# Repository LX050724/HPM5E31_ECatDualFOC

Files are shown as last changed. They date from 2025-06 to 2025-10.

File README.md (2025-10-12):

# 基于HPM5E31的双路EtherCAT高性能高精度FOC驱动板

仓库使用lfs，不能直接下载zip，jlink版本需要v10以上

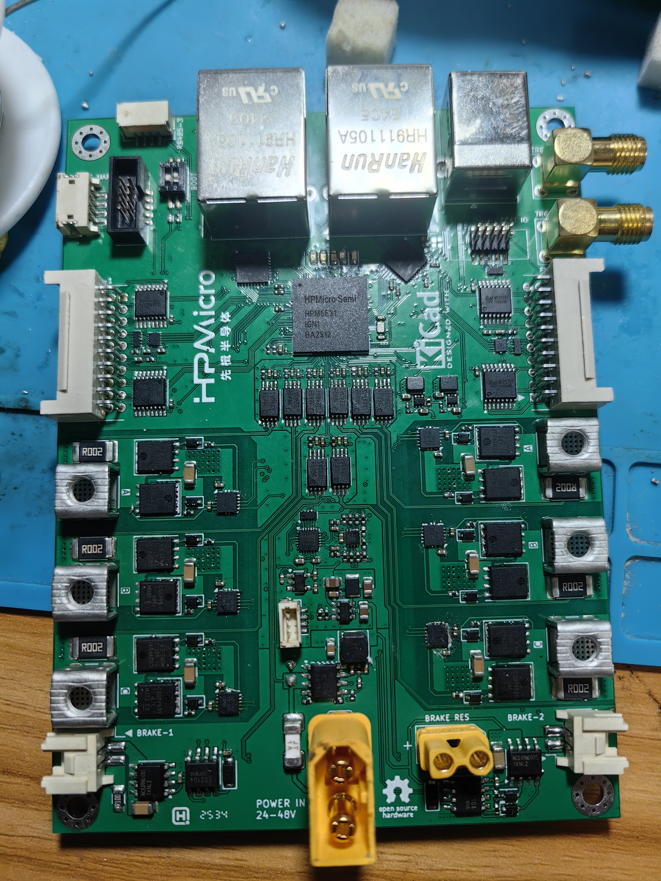
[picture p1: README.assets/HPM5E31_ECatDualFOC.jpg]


## 产品规格：

| 支持电机数 | 2路 |
| --- | --- |
| 动力电源 | 24VDC~60VDC |
| 额定输出电流 | 20Arms |
| 峰值输出电流 | 未测试 |
| 急停按钮 | 光耦输入，支持常开式或常闭式接线或外部电源控制<br />支持硬件安全扭矩关断（SOT） |
| 反馈信号 | 差分ABZ<br />差分UVW<br />基于SPI接口的编码器（抗干扰弱）<br />基于高速485接口的编码器如多摩川<br />电机温度NTC |
| 能耗制动 | 可外接制动电阻 |
| 抱闸 | 支持，最大电流1A，支持电流测量 |
| 冷却方式 | 可选的板载散热器和风扇主动散热 |
| 脉冲方向控制 | 复用ABZ编码器接口可实现PD、UD模式脉冲输入 |
| 模拟量输入 | 不支持 |
| UART | 支持一路调试串口 |
| RS485 | 硬件支持1路专用，2路与485编码器复用 |
| CANFD | 硬件支持2路 |
| EtherCAT | 硬件支持2端口 |
| USB2.0HS | 支持一路Device TypeB接口 |
| 同步信号 | 支持2路TRGM IO，可输入输出PWM同步信号或PPS同步信号等 |
| 存储 | 程序flash 1Mbyte，外置数据qspiflash 128Mbit |

## 电源树：

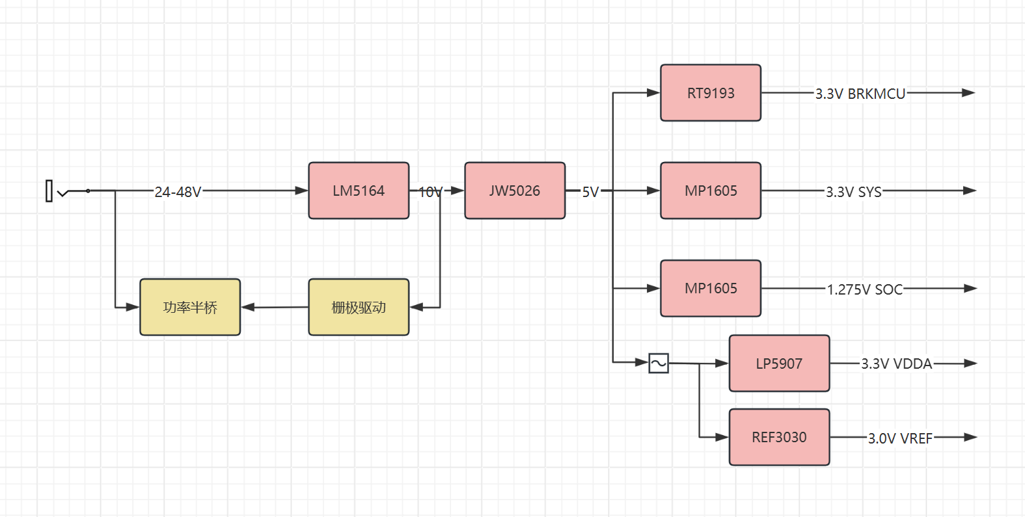
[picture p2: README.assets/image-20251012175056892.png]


## 硬件架构框图：

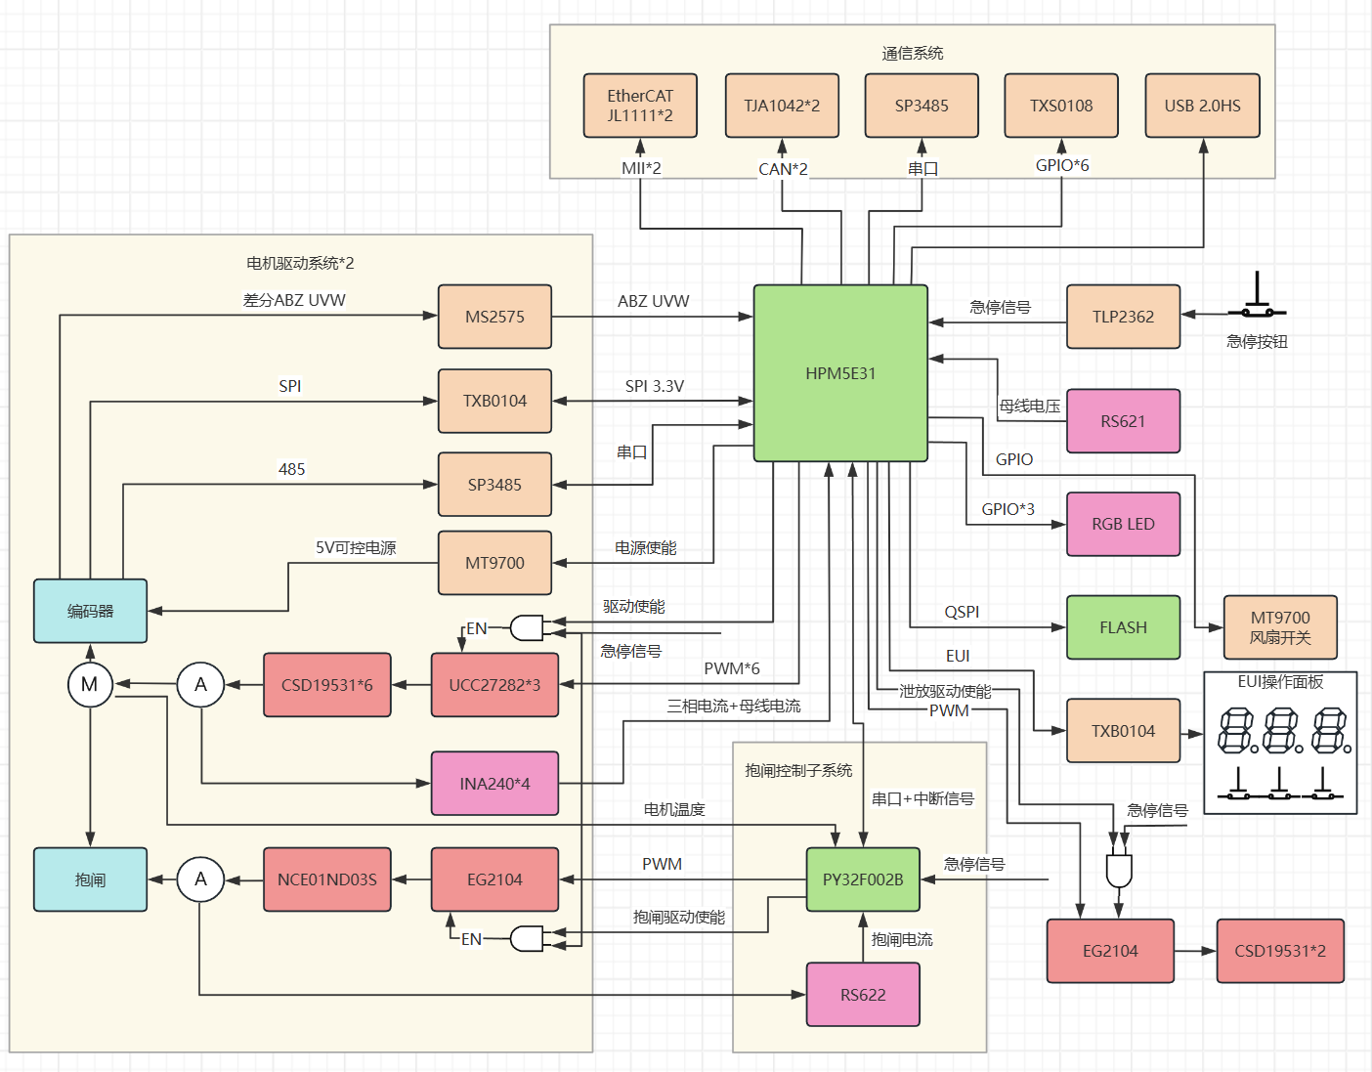
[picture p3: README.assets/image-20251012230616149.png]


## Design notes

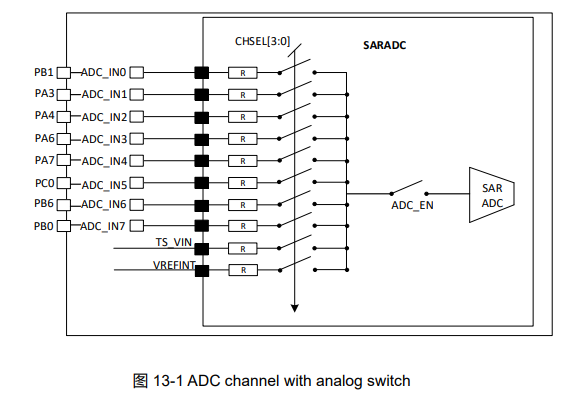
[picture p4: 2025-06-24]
Hardware/PY32F002B_ADCChannel.png

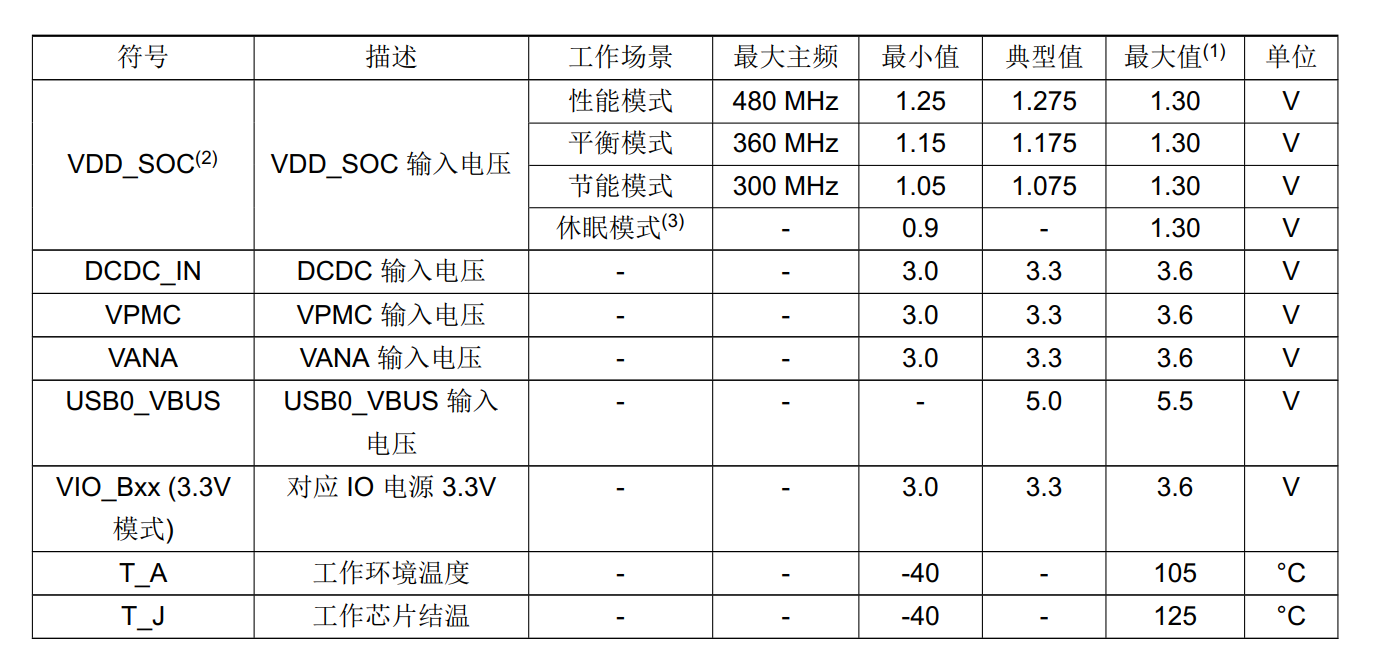
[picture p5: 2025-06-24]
Hardware/HPM5E电压条件.png

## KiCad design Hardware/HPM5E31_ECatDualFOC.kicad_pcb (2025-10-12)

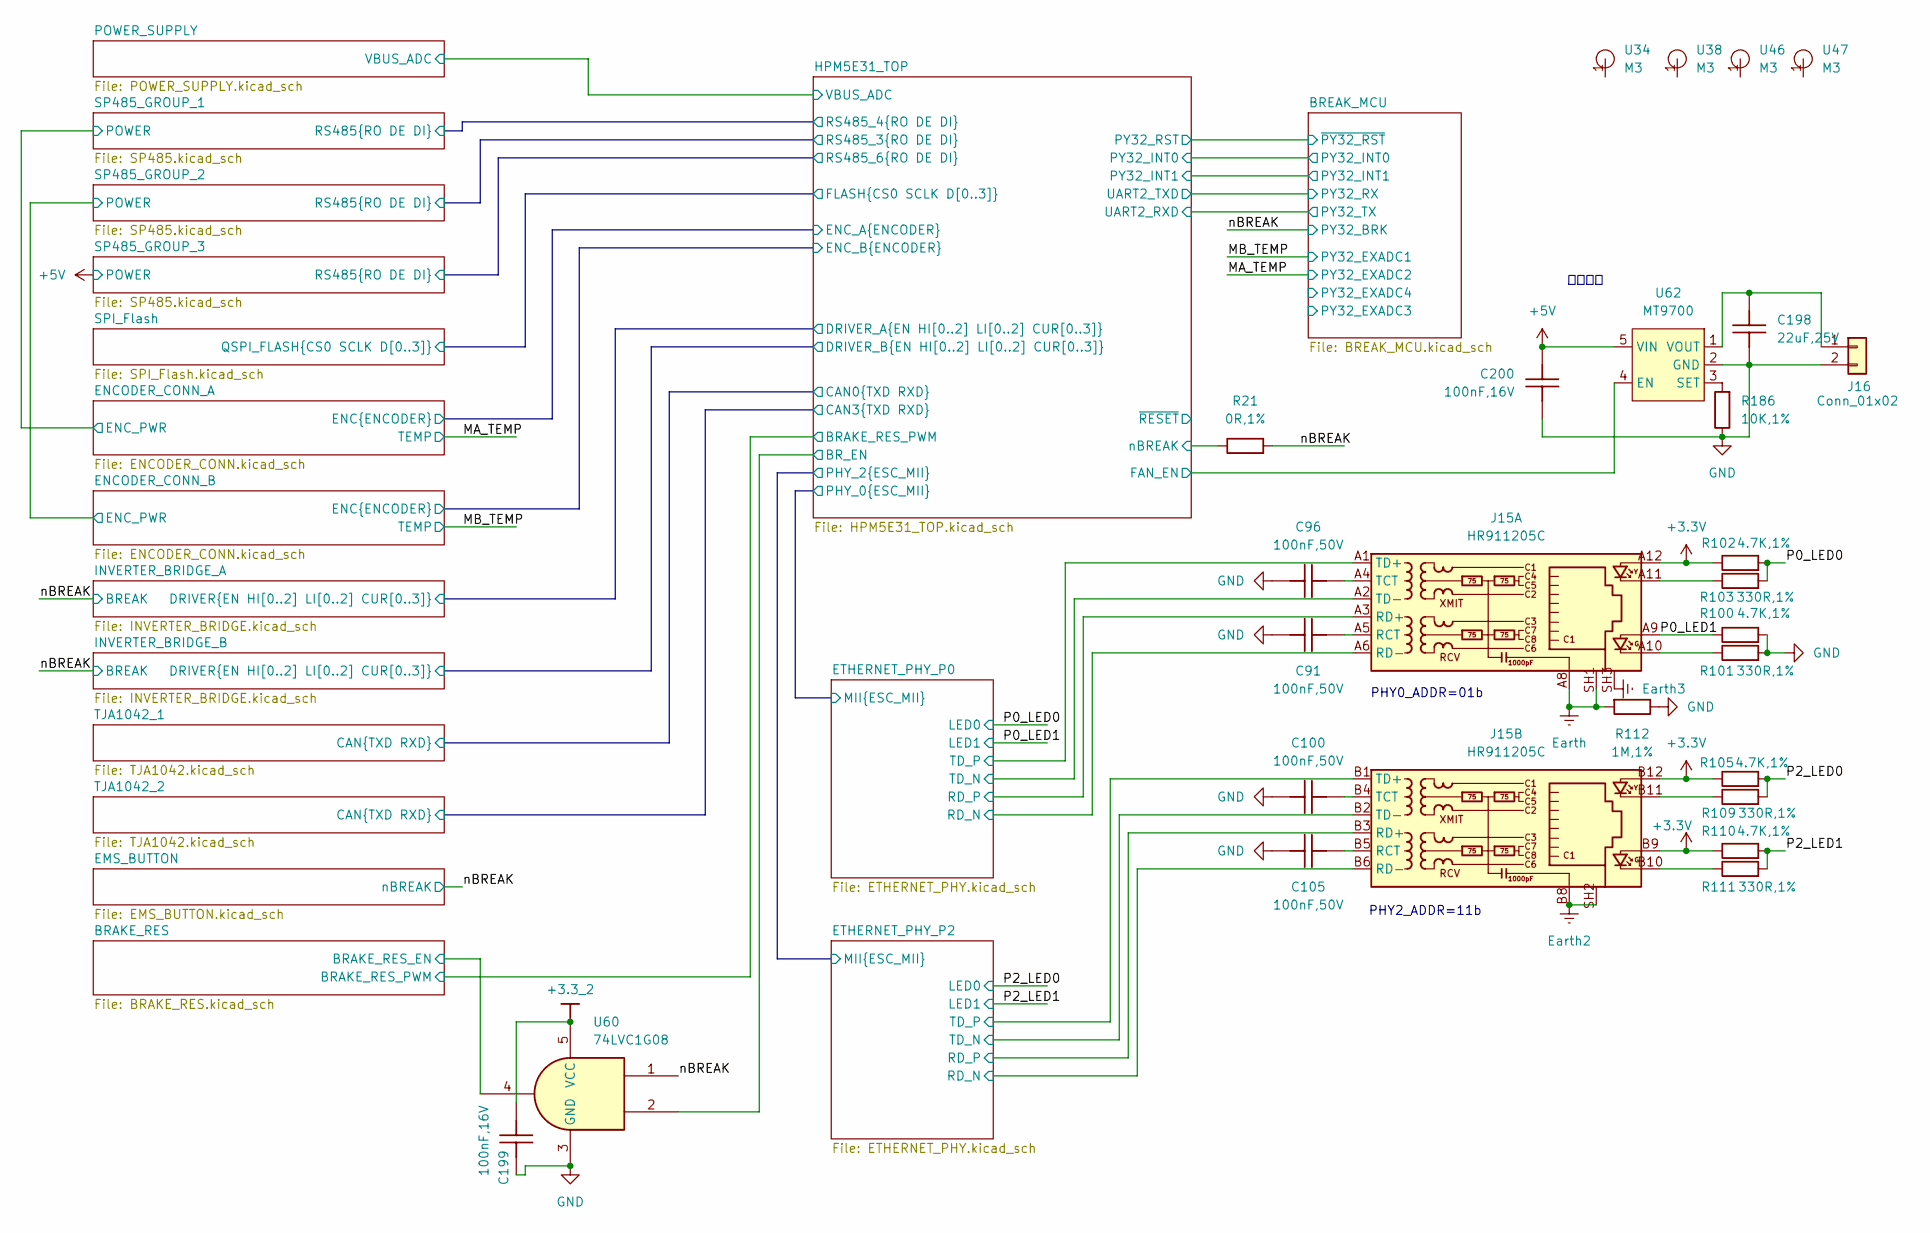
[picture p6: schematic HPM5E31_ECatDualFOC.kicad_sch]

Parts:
C91, C96, C100, C105: 100nF,50V; C_0603_1608Metric
C198: 22uF,25V; C_0805_2012Metric
C199, C200: 100nF,16V; C_0402_1005Metric
J15: HR911205C
J16: Conn_01x02; JST_PH_B2B-PH-K_1x02_P2.00mm_Vertical
R21: 0R,1%; R_0402_1005Metric
R100, R102, R105, R110: 4.7K,1%; R_0402_1005Metric
R101, R103, R109, R111: 330R,1%; R_0402_1005Metric
R112: 1M,1%; R_0805_2012Metric
R186: 10K,1%; R_0402_1005Metric
U34, U38, U46, U47: M3; MountingHole_3.2mm_M3_Pad_Via
U60: 74LVC1G08; SOT-353_SC-70-5
U62: MT9700; SOT-23-5

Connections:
+3.3V: J15.A12, J15.B9, J15.B12, R102.1, R105.1, R110.1; also elsewhere on the board
+3.3_2: C199.1, U60.5 (VCC); also elsewhere on the board
+5V: C200.2, U62.5 (VIN); also elsewhere on the board
/BRAKE_RES/BRAKE_RES_EN: U60.4; also elsewhere on the board
/ETHERNET_PHY_P0/RD_N: J15.A6 (RD-); also elsewhere on the board
/ETHERNET_PHY_P0/RD_P: J15.A3 (RD+); also elsewhere on the board
/ETHERNET_PHY_P0/TD_N: J15.A2 (TD-); also elsewhere on the board
/ETHERNET_PHY_P0/TD_P: J15.A1 (TD+); also elsewhere on the board
/ETHERNET_PHY_P2/RD_N: J15.B6 (RD-); also elsewhere on the board
/ETHERNET_PHY_P2/RD_P: J15.B3 (RD+); also elsewhere on the board
/ETHERNET_PHY_P2/TD_N: J15.B2 (TD-); also elsewhere on the board
/ETHERNET_PHY_P2/TD_P: J15.B1 (TD+); also elsewhere on the board
/P0_LED0: R102.2, R103.2; also elsewhere on the board
/P0_LED1: J15.A9, R100.1; also elsewhere on the board
/P2_LED0: R105.2, R109.2; also elsewhere on the board
/P2_LED1: R110.2, R111.2; also elsewhere on the board
/nBREAK: R21.2, U60.1; also elsewhere on the board
Earth: J15.A8, J15.SH1, R112.2
Earth2: J15.B8, J15.SH2
Earth3: J15.SH3
GND: C91.2, C96.2, C100.2, C105.2, C198.2, C199.2, C200.1, J16.2, R100.2, R101.2, R112.1, R186.1, U60.3 (GND), U62.2 (GND); also elsewhere on the board
unnamed: J15.A10, R101.1
unnamed: J15.A11, R103.1
unnamed: J15.B10, R111.1
unnamed: J15.B11, R109.1
unnamed: C91.1, J15.A5 (RCT)
unnamed: C96.1, J15.A4 (TCT)
unnamed: C105.1, J15.B5 (RCT)
unnamed: C100.1, J15.B4 (TCT)
unnamed: C198.1, J16.1, U62.1 (VOUT)
unnamed: R186.2, U62.3 (SET)
PC10: R21.1; also elsewhere on the board
PF19: U60.2; also elsewhere on the board
PF24: U62.4 (EN); also elsewhere on the board

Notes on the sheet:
PHY2_ADDR=11b
风扇控制
PHY0_ADDR=01b

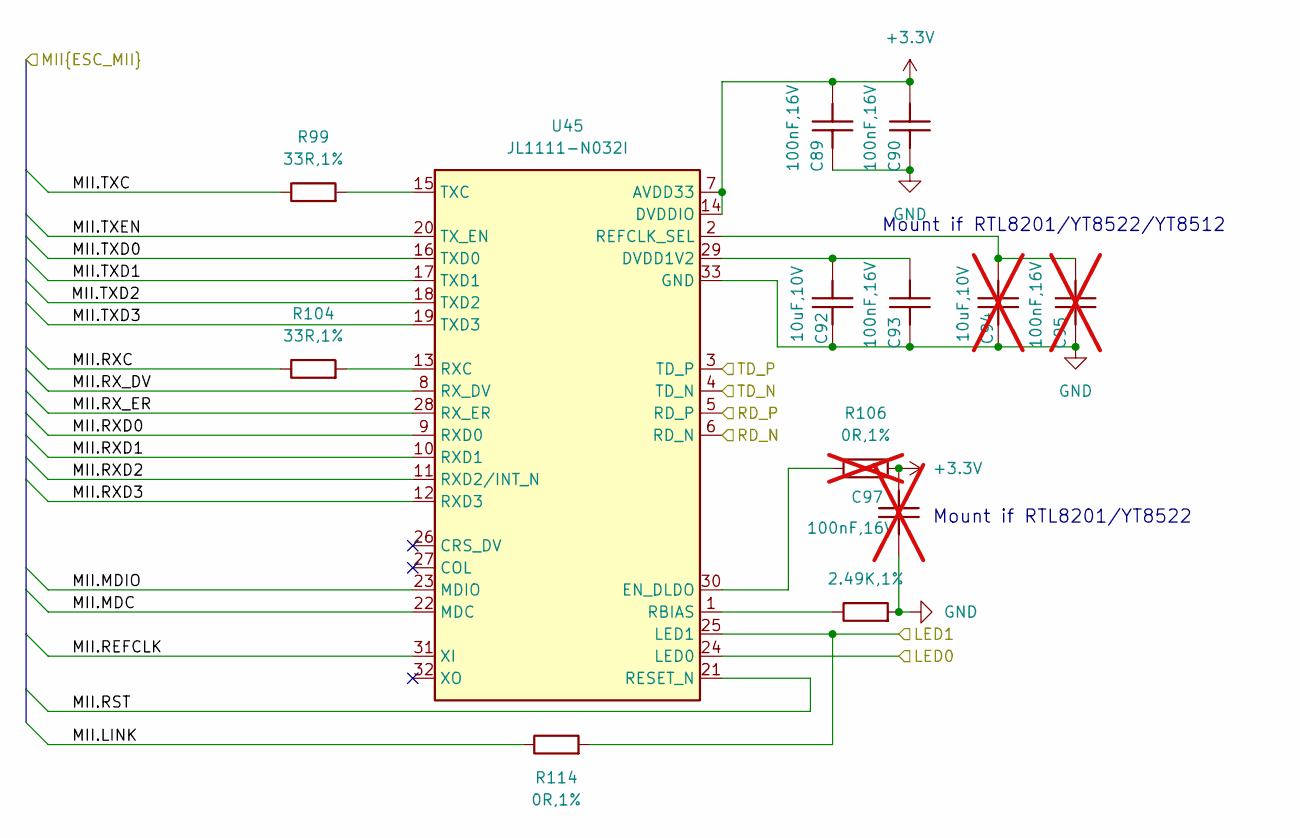
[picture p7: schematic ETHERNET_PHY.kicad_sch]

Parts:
C89, C90, C93: 100nF,16V; C_0402_1005Metric
C92: 10uF,10V; C_0402_1005Metric
C94: 10uF,10V; C_0402_1005Metric; not fitted
C95, C97: 100nF,16V; C_0402_1005Metric; not fitted
R99, R104: 33R,1%; R_0201_0603Metric
R106: 0R,1%; R_0402_1005Metric; not fitted
R107: 2.49K,1%; R_0402_1005Metric
R114: 0R,1%; R_0201_0603Metric
U45: JL1111-N032I; QFN-32-1EP_5x5mm_P0.5mm_EP3.1x3.1mm

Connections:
+3.3V: C89.1, C90.1, C97.1, R106.2, U45.7 (AVDD33), U45.14 (DVDDIO); also elsewhere on the board
/ETHERNET_PHY_P0/MII.LINK: R114.1; also elsewhere on the board
/ETHERNET_PHY_P0/MII.RXC: R104.1; also elsewhere on the board
/ETHERNET_PHY_P0/MII.RXD0: U45.9 (RXD0); also elsewhere on the board
/ETHERNET_PHY_P0/MII.RXD1: U45.10 (RXD1); also elsewhere on the board
/ETHERNET_PHY_P0/MII.RXD2: U45.11 (RXD2/INT_N); also elsewhere on the board
/ETHERNET_PHY_P0/MII.RXD3: U45.12 (RXD3); also elsewhere on the board
/ETHERNET_PHY_P0/MII.RX_DV: U45.8 (RX_DV); also elsewhere on the board
/ETHERNET_PHY_P0/MII.RX_ER: U45.28 (RX_ER); also elsewhere on the board
/ETHERNET_PHY_P0/MII.TXC: R99.1; also elsewhere on the board
/ETHERNET_PHY_P0/MII.TXD0: U45.16 (TXD0); also elsewhere on the board
/ETHERNET_PHY_P0/MII.TXD1: U45.17 (TXD1); also elsewhere on the board
/ETHERNET_PHY_P0/MII.TXD2: U45.18 (TXD2); also elsewhere on the board
/ETHERNET_PHY_P0/MII.TXD3: U45.19 (TXD3); also elsewhere on the board
/ETHERNET_PHY_P0/MII.TXEN: U45.20 (TX_EN); also elsewhere on the board
/ETHERNET_PHY_P0/RD_N: U45.6 (RD_N); also elsewhere on the board
/ETHERNET_PHY_P0/RD_P: U45.5 (RD_P); also elsewhere on the board
/ETHERNET_PHY_P0/TD_N: U45.4 (TD_N); also elsewhere on the board
/ETHERNET_PHY_P0/TD_P: U45.3 (TD_P); also elsewhere on the board
/ETHERNET_PHY_P2/MII.MDC: U45.22 (MDC); also elsewhere on the board
/ETHERNET_PHY_P2/MII.MDIO: U45.23 (MDIO); also elsewhere on the board
/ETHERNET_PHY_P2/MII.REFCLK: U45.31 (XI); also elsewhere on the board
/ETHERNET_PHY_P2/MII.RST: U45.21 (RESET_N); also elsewhere on the board
/P0_LED0: U45.24 (LED0); also elsewhere on the board
/P0_LED1: R114.2, U45.25 (LED1); also elsewhere on the board
GND: C89.2, C90.2, C92.2, C93.2, C94.2, C95.2, C97.2, R107.2, U45.33 (GND); also elsewhere on the board
unnamed: C92.1, C93.1, U45.29 (DVDD1V2)
unnamed: R106.1, U45.30 (EN_DLDO)
unnamed: R107.1, U45.1 (RBIAS)
unnamed: C94.1, C95.1, U45.2 (REFCLK_SEL)
unnamed: R104.2, U45.13 (RXC)
unnamed: R99.2, U45.15 (TXC)

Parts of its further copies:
C98, C99, C102: 100nF,16V; C_0402_1005Metric
C101: 10uF,10V; C_0402_1005Metric
C103: 10uF,10V; C_0402_1005Metric; not fitted
C104, C106: 100nF,16V; C_0402_1005Metric; not fitted
R108, R113: 33R,1%; R_0201_0603Metric
R115: 0R,1%; R_0402_1005Metric; not fitted
R116: 2.49K,1%; R_0402_1005Metric
R183: 0R,1%; R_0201_0603Metric
U48: JL1111-N032I; QFN-32-1EP_5x5mm_P0.5mm_EP3.1x3.1mm

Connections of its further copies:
+3.3V: C98.1, C99.1, C106.1, R115.2, U48.7 (AVDD33), U48.14 (DVDDIO); also elsewhere on the board
/ETHERNET_PHY_P2/MII.LINK: R183.1; also elsewhere on the board
/ETHERNET_PHY_P2/MII.MDC: U48.22 (MDC); also elsewhere on the board
/ETHERNET_PHY_P2/MII.MDIO: U48.23 (MDIO); also elsewhere on the board
/ETHERNET_PHY_P2/MII.REFCLK: U48.31 (XI); also elsewhere on the board
/ETHERNET_PHY_P2/MII.RST: U48.21 (RESET_N); also elsewhere on the board
/ETHERNET_PHY_P2/MII.RXC: R113.1; also elsewhere on the board
/ETHERNET_PHY_P2/MII.RXD0: U48.9 (RXD0); also elsewhere on the board
/ETHERNET_PHY_P2/MII.RXD1: U48.10 (RXD1); also elsewhere on the board
/ETHERNET_PHY_P2/MII.RXD2: U48.11 (RXD2/INT_N); also elsewhere on the board
/ETHERNET_PHY_P2/MII.RXD3: U48.12 (RXD3); also elsewhere on the board
/ETHERNET_PHY_P2/MII.RX_DV: U48.8 (RX_DV); also elsewhere on the board
/ETHERNET_PHY_P2/MII.RX_ER: U48.28 (RX_ER); also elsewhere on the board
/ETHERNET_PHY_P2/MII.TXC: R108.1; also elsewhere on the board
/ETHERNET_PHY_P2/MII.TXD0: U48.16 (TXD0); also elsewhere on the board
/ETHERNET_PHY_P2/MII.TXD1: U48.17 (TXD1); also elsewhere on the board
/ETHERNET_PHY_P2/MII.TXD2: U48.18 (TXD2); also elsewhere on the board
/ETHERNET_PHY_P2/MII.TXD3: U48.19 (TXD3); also elsewhere on the board
/ETHERNET_PHY_P2/MII.TXEN: U48.20 (TX_EN); also elsewhere on the board
/ETHERNET_PHY_P2/RD_N: U48.6 (RD_N); also elsewhere on the board
/ETHERNET_PHY_P2/RD_P: U48.5 (RD_P); also elsewhere on the board
/ETHERNET_PHY_P2/TD_N: U48.4 (TD_N); also elsewhere on the board
/ETHERNET_PHY_P2/TD_P: U48.3 (TD_P); also elsewhere on the board
/P2_LED0: U48.24 (LED0); also elsewhere on the board
/P2_LED1: R183.2, U48.25 (LED1); also elsewhere on the board
GND: C98.2, C99.2, C101.2, C102.2, C103.2, C104.2, C106.2, R116.2, U48.33 (GND); also elsewhere on the board
unnamed: C101.1, C102.1, U48.29 (DVDD1V2)
unnamed: R115.1, U48.30 (EN_DLDO)
unnamed: R116.1, U48.1 (RBIAS)
unnamed: C103.1, C104.1, U48.2 (REFCLK_SEL)
unnamed: R113.2, U48.13 (RXC)
unnamed: R108.2, U48.15 (TXC)

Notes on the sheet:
Mount if RTL8201/YT8522
Mount if RTL8201/YT8522/YT8512

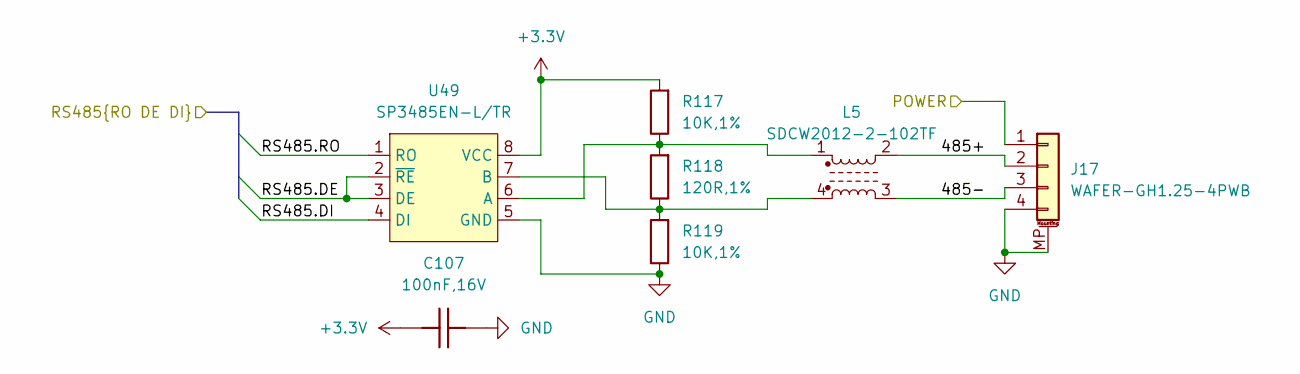
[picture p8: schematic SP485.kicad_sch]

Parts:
C107: 100nF,16V; C_0402_1005Metric
J17: WAFER-GH1.25-4PWB; JST_GH_SM04B-GHS-TB_1x04-1MP_P1.25mm_Horizontal
L5: SDCW2012-2-102TF; L_CommonModeChoke_Coilcraft_0805USB
R117, R119: 10K,1%; R_0402_1005Metric
R118: 120R,1%; R_0603_1608Metric
U49: SP3485EN-L/TR; SOIC-8_3.9x4.9mm_P1.27mm

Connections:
+3.3V: C107.1, R117.2, U49.8 (VCC); also elsewhere on the board
/ENCODER_CONN_A/ENC_PWR: J17.1; also elsewhere on the board
/HPM5E31_TOP/RS485_4.DE: U49.2 (~RE), U49.3 (DE); also elsewhere on the board
/HPM5E31_TOP/RS485_4.DI: U49.4 (DI); also elsewhere on the board
/HPM5E31_TOP/RS485_4.RO: U49.1 (RO); also elsewhere on the board
/SP485_GROUP_1/485+: J17.2, L5.2
/SP485_GROUP_1/485-: J17.3, L5.3
GND: C107.2, J17.4, J17.MP (MountPin), R119.1, U49.5 (GND); also elsewhere on the board
unnamed: L5.1, R117.1, R118.2, U49.6 (A)
unnamed: L5.4, R118.1, R119.2, U49.7 (B)

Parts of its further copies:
C108, C109: 100nF,16V; C_0402_1005Metric
J18, J19: WAFER-GH1.25-4PWB; JST_GH_SM04B-GHS-TB_1x04-1MP_P1.25mm_Horizontal
L6, L7: SDCW2012-2-102TF; L_CommonModeChoke_Coilcraft_0805USB
R120, R122, R123, R125: 10K,1%; R_0402_1005Metric
R121, R124: 120R,1%; R_0603_1608Metric
U50, U51: SP3485EN-L/TR; SOIC-8_3.9x4.9mm_P1.27mm

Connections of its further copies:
+3.3V: C108.1, C109.1, R120.2, R123.2, U50.8 (VCC), U51.8 (VCC); also elsewhere on the board
+5V: J19.1; also elsewhere on the board
/ENCODER_CONN_B/ENC_PWR: J18.1; also elsewhere on the board
/HPM5E31_TOP/RS485_3.DE: U50.2 (~RE), U50.3 (DE); also elsewhere on the board
/HPM5E31_TOP/RS485_3.DI: U50.4 (DI); also elsewhere on the board
/HPM5E31_TOP/RS485_3.RO: U50.1 (RO); also elsewhere on the board
/HPM5E31_TOP/RS485_6.DE: U51.2 (~RE), U51.3 (DE); also elsewhere on the board
/HPM5E31_TOP/RS485_6.DI: U51.4 (DI); also elsewhere on the board
/HPM5E31_TOP/RS485_6.RO: U51.1 (RO); also elsewhere on the board
/SP485_GROUP_2/485+: J18.2, L6.2
/SP485_GROUP_2/485-: J18.3, L6.3
/SP485_GROUP_3/485+: J19.2, L7.2
/SP485_GROUP_3/485-: J19.3, L7.3
GND: C108.2, C109.2, J18.4, J18.MP (MountPin), J19.4, J19.MP (MountPin), R122.1, R125.1, U50.5 (GND), U51.5 (GND); also elsewhere on the board
unnamed: L6.1, R120.1, R121.2, U50.6 (A)
unnamed: L6.4, R121.1, R122.2, U50.7 (B)
unnamed: L7.1, R123.1, R124.2, U51.6 (A)
unnamed: L7.4, R124.1, R125.2, U51.7 (B)

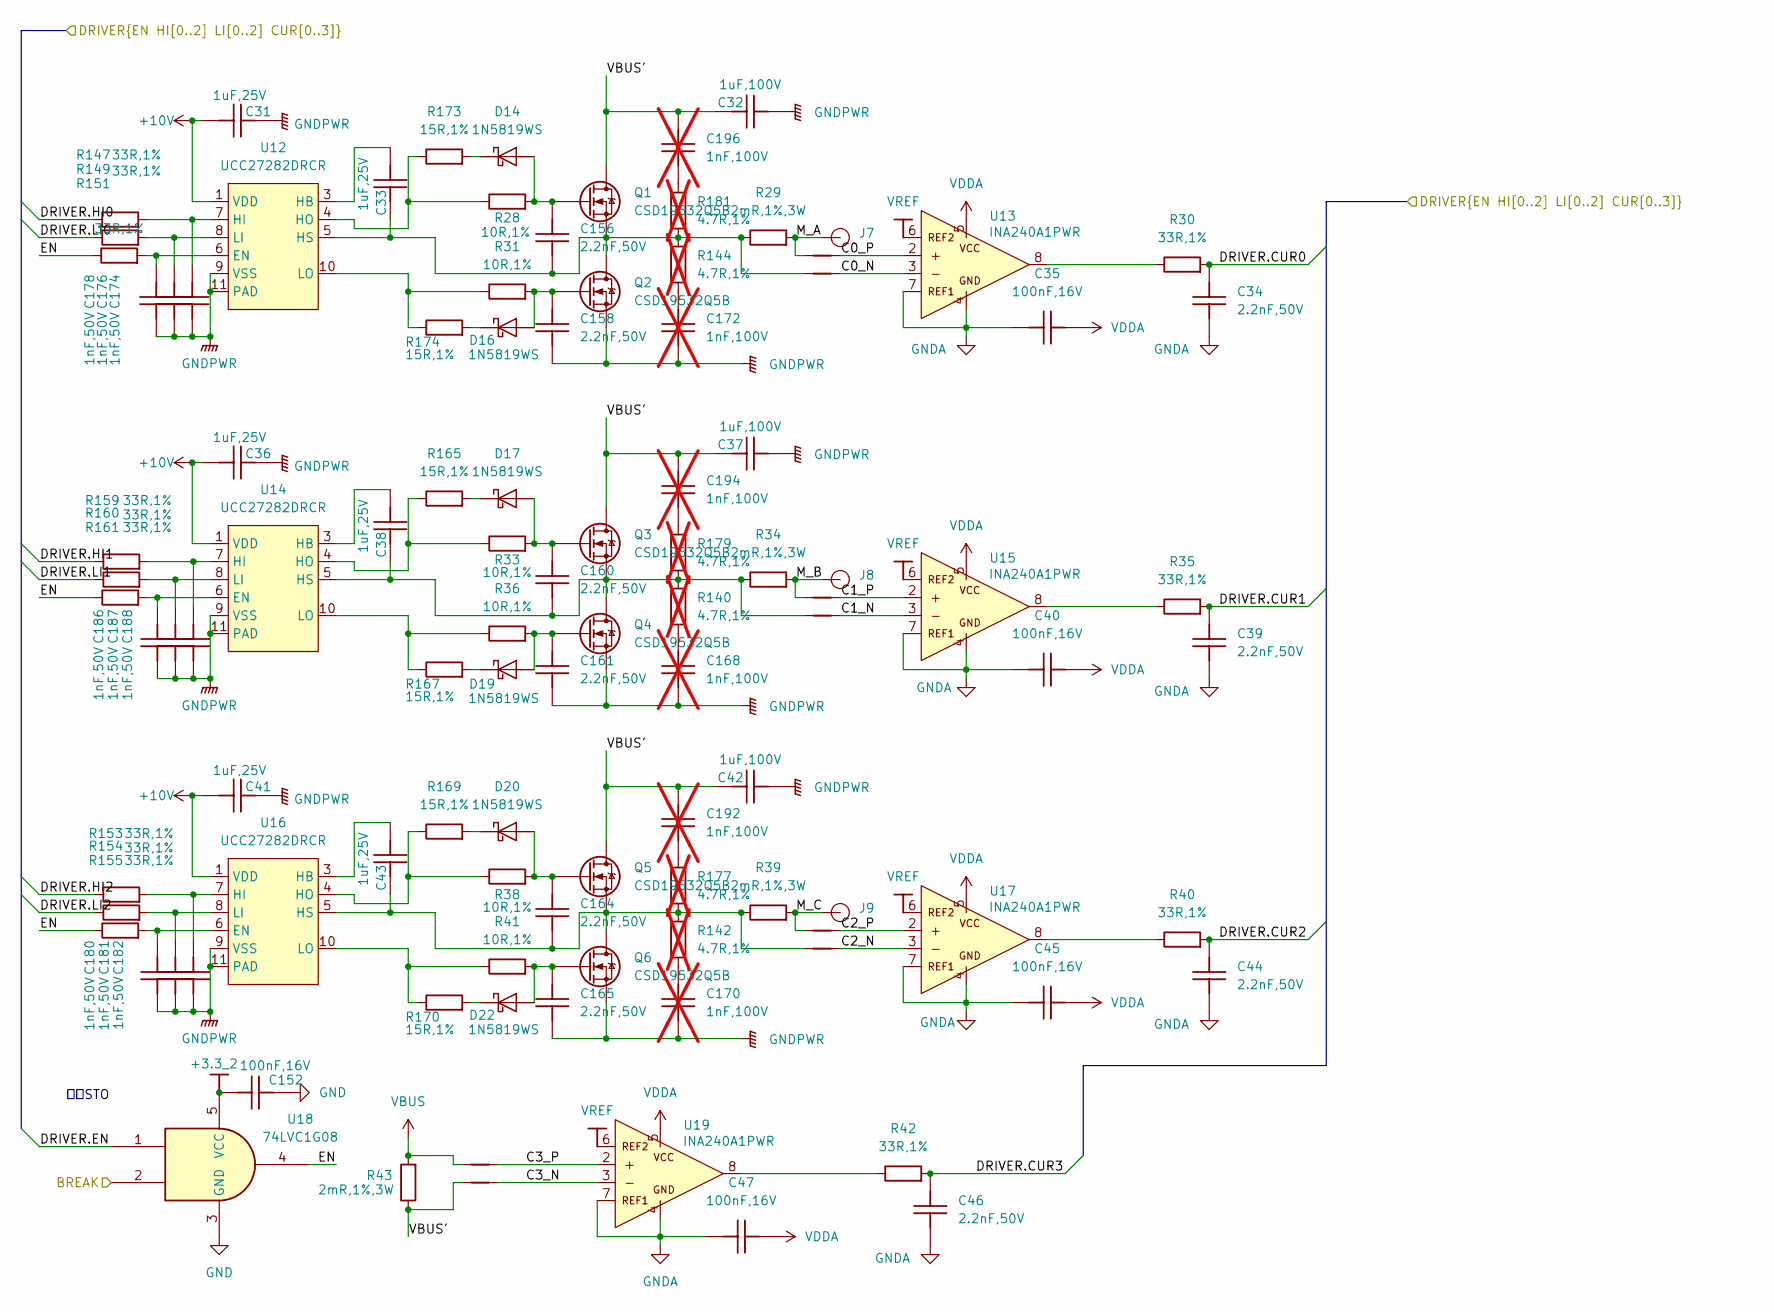
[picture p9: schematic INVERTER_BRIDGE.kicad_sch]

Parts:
C31, C33, C36, C38, C41, C43: 1uF,25V; C_0402_1005Metric
C32, C37, C42: 1uF,100V; C_1206_3216Metric
C34, C39, C44, C46, C156, C158, C160, C161, C164, C165: 2.2nF,50V; C_0402_1005Metric
C35, C40, C45, C47, C152: 100nF,16V; C_0402_1005Metric
C168, C170, C172, C192, C194, C196: 1nF,100V; C_0603_1608Metric; not fitted
C174, C176, C178, C180, C181, C182, C186, C187, C188: 1nF,50V; C_0201_0603Metric
D14, D16, D17, D19, D20, D22: 1N5819WS; D_SOD-323
J7, J8, J9: YZ-1
NT1, NT2, NT3, NT4, NT5, NT6, NT7, NT8: NetTie_2; NetTie_SMD_5mil
Q1, Q2, Q3, Q4, Q5, Q6: CSD19532Q5B; PQFN-8-EP_6x5mm_P1.27mm_Generic
R28, R31, R33, R36, R38, R41: 10R,1%; R_0402_1005Metric
R29, R34, R39, R43: 2mR,1%,3W; R_2512_6332Metric
R30, R35, R40, R42: 33R,1%; R_0402_1005Metric
R140, R142, R144, R177, R179, R181: 4.7R,1%; R_0603_1608Metric; not fitted
R147, R149, R151, R153, R154, R155, R159, R160, R161: 33R,1%; R_0201_0603Metric
R165, R167, R169, R170, R173, R174: 15R,1%; R_0402_1005Metric
U12, U14, U16: UCC27282DRCR; VSON-10-1EP_3x3mm_P0.5mm_EP1.65x2.4mm
U13, U15, U17, U19: INA240A1PWR; TSSOP-8_4.4x3mm_P0.65mm
U18: 74LVC1G08; SOT-353_SC-70-5

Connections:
+3.3_2: C152.2, U18.5 (VCC); also elsewhere on the board
+10V: C31.1, C36.1, C41.1, U12.1 (VDD), U14.1 (VDD), U16.1 (VDD); also elsewhere on the board
/HPM5E31_TOP/DRIVER_B.CUR0: C34.1, R30.2; also elsewhere on the board
/HPM5E31_TOP/DRIVER_B.CUR1: C39.1, R35.2; also elsewhere on the board
/HPM5E31_TOP/DRIVER_B.CUR2: C44.1, R40.2; also elsewhere on the board
/HPM5E31_TOP/DRIVER_B.CUR3: C46.1, R42.2; also elsewhere on the board
/HPM5E31_TOP/DRIVER_B.EN: U18.1; also elsewhere on the board
/HPM5E31_TOP/DRIVER_B.HI0: R147.1; also elsewhere on the board
/HPM5E31_TOP/DRIVER_B.HI1: R159.1; also elsewhere on the board
/HPM5E31_TOP/DRIVER_B.HI2: R153.1; also elsewhere on the board
/HPM5E31_TOP/DRIVER_B.LI0: R149.1; also elsewhere on the board
/HPM5E31_TOP/DRIVER_B.LI1: R160.1; also elsewhere on the board
/HPM5E31_TOP/DRIVER_B.LI2: R154.1; also elsewhere on the board
/INVERTER_BRIDGE_B/C0_N: NT2.2, U13.3 (IN-)
/INVERTER_BRIDGE_B/C0_P: NT1.2, U13.2 (IN+)
/INVERTER_BRIDGE_B/C1_N: NT4.2, U15.3 (IN-)
/INVERTER_BRIDGE_B/C1_P: NT3.2, U15.2 (IN+)
/INVERTER_BRIDGE_B/C2_N: NT6.2, U17.3 (IN-)
/INVERTER_BRIDGE_B/C2_P: NT5.2, U17.2 (IN+)
/INVERTER_BRIDGE_B/C3_N: NT8.2, U19.3 (IN-)
/INVERTER_BRIDGE_B/C3_P: NT7.2, U19.2 (IN+)
/INVERTER_BRIDGE_B/EN: R151.1, R155.1, R161.1, U18.4
/INVERTER_BRIDGE_B/M_A: J7.1, NT1.1, R29.2
/INVERTER_BRIDGE_B/M_B: J8.1, NT3.1, R34.2
/INVERTER_BRIDGE_B/M_C: J9.1, NT5.1, R39.2
/INVERTER_BRIDGE_B/VBUS': C32.1, C37.1, C42.1, C192.1, C194.1, C196.1, NT8.1, Q1.1 (D), Q3.1 (D), Q5.1 (D), R43.1
/nBREAK: U18.2; also elsewhere on the board
GND: C152.1, U18.3 (GND); also elsewhere on the board
GNDA: C34.2, C35.2, C39.2, C40.2, C44.2, C45.2, C46.2, C47.2, U13.4 (GND), U13.7 (REF1), U15.4 (GND), U15.7 (REF1), U17.4 (GND), U17.7 (REF1), U19.4 (GND), U19.7 (REF1); also elsewhere on the board
GNDPWR: C31.2, C32.2, C36.2, C37.2, C41.2, C42.2, C158.2, C161.2, C165.2, C168.2, C170.2, C172.2, C174.2, C176.2, C178.2, C180.2, C181.2, C182.2, C186.2, C187.2, C188.2, Q2.3 (S), Q4.3 (S), Q6.3 (S), U12.9 (VSS), U12.11 (PAD), U14.9 (VSS), U14.11 (PAD), U16.9 (VSS), U16.11 (PAD); also elsewhere on the board
unnamed: C168.1, R140.1
unnamed: C170.1, R142.1
unnamed: C172.1, R144.1
unnamed: C192.2, R177.2
unnamed: C194.2, R179.2
unnamed: C196.2, R181.2
unnamed: C156.1, D14.2 (A), Q1.2 (G), R28.2
unnamed: D14.1 (K), R173.2
unnamed: C158.1, D16.2 (A), Q2.2 (G), R31.2
unnamed: D16.1 (K), R174.2
unnamed: C160.1, D17.2 (A), Q3.2 (G), R33.2
unnamed: D17.1 (K), R165.2
unnamed: C161.1, D19.2 (A), Q4.2 (G), R36.2
unnamed: D19.1 (K), R167.2
unnamed: C164.1, D20.2 (A), Q5.2 (G), R38.2
unnamed: D20.1 (K), R169.2
unnamed: C165.1, D22.2 (A), Q6.2 (G), R41.2
unnamed: D22.1 (K), R170.2
unnamed: C33.2, C156.2, NT2.1, Q1.3 (S), Q2.1 (D), R29.1, R144.2, R181.1, U12.5 (HS)
unnamed: C38.2, C160.2, NT4.1, Q3.3 (S), Q4.1 (D), R34.1, R140.2, R179.1, U14.5 (HS)
unnamed: C43.2, C164.2, NT6.1, Q5.3 (S), Q6.1 (D), R39.1, R142.2, R177.1, U16.5 (HS)
unnamed: C178.1, R151.2, U12.6 (EN)
unnamed: C33.1, U12.3 (HB)
unnamed: C174.1, R147.2, U12.7 (HI)
unnamed: R28.1, R173.1, U12.4 (HO)
unnamed: C176.1, R149.2, U12.8 (LI)
unnamed: R31.1, R174.1, U12.10 (LO)
unnamed: R30.1, U13.8 (OUT)
unnamed: C186.1, R161.2, U14.6 (EN)
unnamed: C38.1, U14.3 (HB)
unnamed: C188.1, R159.2, U14.7 (HI)
unnamed: R33.1, R165.1, U14.4 (HO)
unnamed: C187.1, R160.2, U14.8 (LI)
unnamed: R36.1, R167.1, U14.10 (LO)
unnamed: R35.1, U15.8 (OUT)
unnamed: C180.1, R155.2, U16.6 (EN)
unnamed: C43.1, U16.3 (HB)
unnamed: C182.1, R153.2, U16.7 (HI)
unnamed: R38.1, R169.1, U16.4 (HO)
unnamed: C181.1, R154.2, U16.8 (LI)
unnamed: R41.1, R170.1, U16.10 (LO)
unnamed: R40.1, U17.8 (OUT)
unnamed: R42.1, U19.8 (OUT)
VBUS: NT7.1, R43.2; also elsewhere on the board
VDDA: C35.1, C40.1, C45.1, C47.1, U13.5 (VS), U15.5 (VS), U17.5 (VS), U19.5 (VS); also elsewhere on the board
VREF: U13.6 (REF2), U15.6 (REF2), U17.6 (REF2), U19.6 (REF2); also elsewhere on the board

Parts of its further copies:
C48, C50, C53, C55, C58, C60: 1uF,25V; C_0402_1005Metric
C49, C54, C59: 1uF,100V; C_1206_3216Metric
C51, C56, C61, C63, C157, C159, C162, C163, C166, C167: 2.2nF,50V; C_0402_1005Metric
C52, C57, C62, C64, C153: 100nF,16V; C_0402_1005Metric
C169, C171, C173, C193, C195, C197: 1nF,100V; C_0603_1608Metric; not fitted
C175, C177, C179, C183, C184, C185, C189, C190, C191: 1nF,50V; C_0201_0603Metric
D23, D25, D26, D28, D29, D31: 1N5819WS; D_SOD-323
J10, J11, J12: YZ-1
NT9, NT10, NT11, NT12, NT13, NT14, NT15, NT16: NetTie_2; NetTie_SMD_5mil
Q7, Q8, Q9, Q10, Q11, Q12: CSD19532Q5B; PQFN-8-EP_6x5mm_P1.27mm_Generic
R45, R48, R50, R53, R55, R58: 10R,1%; R_0402_1005Metric
R46, R51, R56, R60: 2mR,1%,3W; R_2512_6332Metric
R47, R52, R57, R59: 33R,1%; R_0402_1005Metric
R141, R143, R145, R178, R180, R182: 4.7R,1%; R_0603_1608Metric; not fitted
R148, R150, R152, R156, R157, R158, R162, R163, R164: 33R,1%; R_0201_0603Metric
R166, R168, R171, R172, R175, R176: 15R,1%; R_0402_1005Metric
U20, U22, U24: UCC27282DRCR; VSON-10-1EP_3x3mm_P0.5mm_EP1.65x2.4mm
U21, U23, U25, U27: INA240A1PWR; TSSOP-8_4.4x3mm_P0.65mm
U26: 74LVC1G08; SOT-353_SC-70-5

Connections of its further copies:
+3.3_2: C153.2, U26.5 (VCC); also elsewhere on the board
+10V: C48.1, C53.1, C58.1, U20.1 (VDD), U22.1 (VDD), U24.1 (VDD); also elsewhere on the board
/HPM5E31_TOP/DRIVER_A.CUR0: C51.1, R47.2; also elsewhere on the board
/HPM5E31_TOP/DRIVER_A.CUR1: C56.1, R52.2; also elsewhere on the board
/HPM5E31_TOP/DRIVER_A.CUR2: C61.1, R57.2; also elsewhere on the board
/HPM5E31_TOP/DRIVER_A.CUR3: C63.1, R59.2; also elsewhere on the board
/HPM5E31_TOP/DRIVER_A.EN: U26.1; also elsewhere on the board
/HPM5E31_TOP/DRIVER_A.HI0: R148.1; also elsewhere on the board
/HPM5E31_TOP/DRIVER_A.HI1: R162.1; also elsewhere on the board
/HPM5E31_TOP/DRIVER_A.HI2: R156.1; also elsewhere on the board
/HPM5E31_TOP/DRIVER_A.LI0: R150.1; also elsewhere on the board
/HPM5E31_TOP/DRIVER_A.LI1: R163.1; also elsewhere on the board
/HPM5E31_TOP/DRIVER_A.LI2: R157.1; also elsewhere on the board
/INVERTER_BRIDGE_A/C0_N: NT10.2, U21.3 (IN-)
/INVERTER_BRIDGE_A/C0_P: NT9.2, U21.2 (IN+)
/INVERTER_BRIDGE_A/C1_N: NT12.2, U23.3 (IN-)
/INVERTER_BRIDGE_A/C1_P: NT11.2, U23.2 (IN+)
/INVERTER_BRIDGE_A/C2_N: NT14.2, U25.3 (IN-)
/INVERTER_BRIDGE_A/C2_P: NT13.2, U25.2 (IN+)
/INVERTER_BRIDGE_A/C3_N: NT16.2, U27.3 (IN-)
/INVERTER_BRIDGE_A/C3_P: NT15.2, U27.2 (IN+)
/INVERTER_BRIDGE_A/EN: R152.1, R158.1, R164.1, U26.4
/INVERTER_BRIDGE_A/M_A: J10.1, NT9.1, R46.2
/INVERTER_BRIDGE_A/M_B: J11.1, NT11.1, R51.2
/INVERTER_BRIDGE_A/M_C: J12.1, NT13.1, R56.2
/INVERTER_BRIDGE_A/VBUS': C49.1, C54.1, C59.1, C193.1, C195.1, C197.1, NT16.1, Q7.1 (D), Q9.1 (D), Q11.1 (D), R60.1
/nBREAK: U26.2; also elsewhere on the board
GND: C153.1, U26.3 (GND); also elsewhere on the board
GNDA: C51.2, C52.2, C56.2, C57.2, C61.2, C62.2, C63.2, C64.2, U21.4 (GND), U21.7 (REF1), U23.4 (GND), U23.7 (REF1), U25.4 (GND), U25.7 (REF1), U27.4 (GND), U27.7 (REF1); also elsewhere on the board
GNDPWR: C48.2, C49.2, C53.2, C54.2, C58.2, C59.2, C159.2, C163.2, C167.2, C169.2, C171.2, C173.2, C175.2, C177.2, C179.2, C183.2, C184.2, C185.2, C189.2, C190.2, C191.2, Q8.3 (S), Q10.3 (S), Q12.3 (S), U20.9 (VSS), U20.11 (PAD), U22.9 (VSS), U22.11 (PAD), U24.9 (VSS), U24.11 (PAD); also elsewhere on the board
unnamed: C169.1, R141.1
unnamed: C171.1, R143.1
unnamed: C173.1, R145.1
unnamed: C193.2, R178.2
unnamed: C195.2, R180.2
unnamed: C197.2, R182.2
unnamed: C157.1, D23.2 (A), Q7.2 (G), R45.2
unnamed: D23.1 (K), R175.2
unnamed: C159.1, D25.2 (A), Q8.2 (G), R48.2
unnamed: D25.1 (K), R176.2
unnamed: C162.1, D26.2 (A), Q9.2 (G), R50.2
unnamed: D26.1 (K), R166.2
unnamed: C163.1, D28.2 (A), Q10.2 (G), R53.2
unnamed: D28.1 (K), R168.2
unnamed: C166.1, D29.2 (A), Q11.2 (G), R55.2
unnamed: D29.1 (K), R171.2
unnamed: C167.1, D31.2 (A), Q12.2 (G), R58.2
unnamed: D31.1 (K), R172.2
unnamed: C50.2, C157.2, NT10.1, Q7.3 (S), Q8.1 (D), R46.1, R145.2, R182.1, U20.5 (HS)
unnamed: C55.2, C162.2, NT12.1, Q9.3 (S), Q10.1 (D), R51.1, R141.2, R180.1, U22.5 (HS)
unnamed: C60.2, C166.2, NT14.1, Q11.3 (S), Q12.1 (D), R56.1, R143.2, R178.1, U24.5 (HS)
unnamed: C179.1, R152.2, U20.6 (EN)
unnamed: C50.1, U20.3 (HB)
unnamed: C175.1, R148.2, U20.7 (HI)
unnamed: R45.1, R175.1, U20.4 (HO)
unnamed: C177.1, R150.2, U20.8 (LI)
unnamed: R48.1, R176.1, U20.10 (LO)
unnamed: R47.1, U21.8 (OUT)
unnamed: C189.1, R164.2, U22.6 (EN)
unnamed: C55.1, U22.3 (HB)
unnamed: C191.1, R162.2, U22.7 (HI)
unnamed: R50.1, R166.1, U22.4 (HO)
unnamed: C190.1, R163.2, U22.8 (LI)
unnamed: R53.1, R168.1, U22.10 (LO)
unnamed: R52.1, U23.8 (OUT)
unnamed: C183.1, R158.2, U24.6 (EN)
unnamed: C60.1, U24.3 (HB)
unnamed: C185.1, R156.2, U24.7 (HI)
unnamed: R55.1, R171.1, U24.4 (HO)
unnamed: C184.1, R157.2, U24.8 (LI)
unnamed: R58.1, R172.1, U24.10 (LO)
unnamed: R57.1, U25.8 (OUT)
unnamed: R59.1, U27.8 (OUT)
VBUS: NT15.1, R60.2; also elsewhere on the board
VDDA: C52.1, C57.1, C62.1, C64.1, U21.5 (VS), U23.5 (VS), U25.5 (VS), U27.5 (VS); also elsewhere on the board
VREF: U21.6 (REF2), U23.6 (REF2), U25.6 (REF2), U27.6 (REF2); also elsewhere on the board

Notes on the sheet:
硬件STO

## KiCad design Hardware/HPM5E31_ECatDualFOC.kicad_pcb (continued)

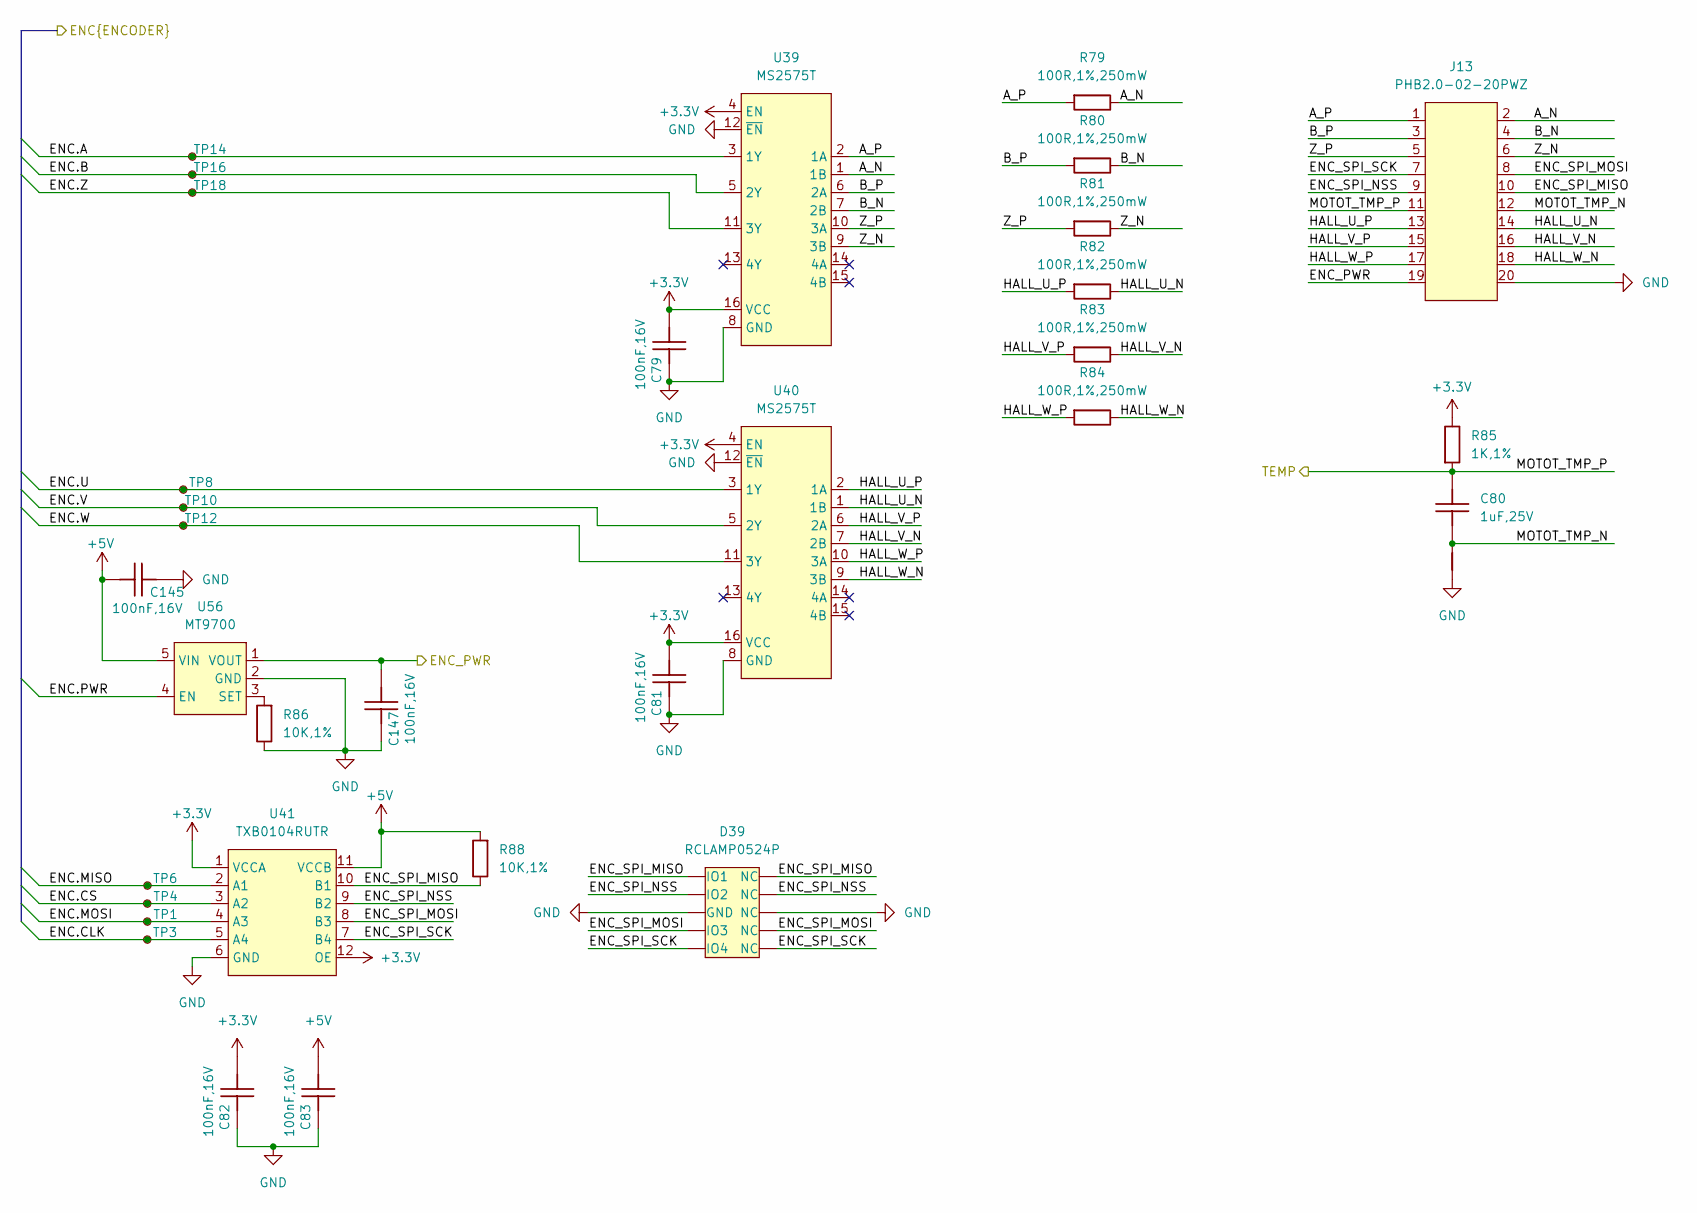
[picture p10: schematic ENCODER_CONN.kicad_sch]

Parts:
C79, C81, C82, C83, C145, C147: 100nF,16V; C_0402_1005Metric
C80: 1uF,25V; C_0402_1005Metric
D39: RCLAMP0524P; Diodes_UDFN-10_1.0x2.5mm_P0.5mm
J13: PHB2.0-02-20PWZ
NT21: NetTie_2; NetTie_SMD_5mil
R79, R80, R81, R82, R83, R84: 100R,1%,250mW; R_0603_1608Metric
R85: 1K,1%; R_0402_1005Metric
R86, R88: 10K,1%; R_0402_1005Metric
TP1, TP3, TP4, TP6, TP8, TP10, TP12, TP14, TP16, TP18: test_point_0.5mm
U39, U40: MS2575T; TSSOP-16_4.4x5mm_P0.65mm
U41: TXB0104RUTR; UQFN-12_1.7x2_Pitch0.4mm
U56: MT9700; SOT-23-5

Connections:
+3.3V: C79.1, C81.1, C82.1, R85.1, U39.4 (EN), U39.16 (VCC), U40.4 (EN), U40.16 (VCC), U41.1 (VCCA), U41.12 (OE); also elsewhere on the board
+5V: C83.1, C145.1, R88.2, U41.11 (VCCB), U56.5 (VIN); also elsewhere on the board
/ENCODER_CONN_A/A_N: J13.2, R79.1, U39.1 (1B)
/ENCODER_CONN_A/A_P: J13.1, R79.2, U39.2 (1A)
/ENCODER_CONN_A/B_N: J13.4, R80.1, U39.7 (2B)
/ENCODER_CONN_A/B_P: J13.3, R80.2, U39.6 (2A)
/ENCODER_CONN_A/ENC.A: TP14.1, U39.3 (1Y); also elsewhere on the board
/ENCODER_CONN_A/ENC.B: TP16.1, U39.5 (2Y); also elsewhere on the board
/ENCODER_CONN_A/ENC.CLK: TP3.1, U41.5 (A4); also elsewhere on the board
/ENCODER_CONN_A/ENC.CS: TP4.1, U41.3 (A2); also elsewhere on the board
/ENCODER_CONN_A/ENC.MISO: TP6.1, U41.2 (A1); also elsewhere on the board
/ENCODER_CONN_A/ENC.MOSI: TP1.1, U41.4 (A3); also elsewhere on the board
/ENCODER_CONN_A/ENC.PWR: U56.4 (EN); also elsewhere on the board
/ENCODER_CONN_A/ENC.U: TP8.1, U40.3 (1Y); also elsewhere on the board
/ENCODER_CONN_A/ENC.V: TP10.1, U40.5 (2Y); also elsewhere on the board
/ENCODER_CONN_A/ENC.W: TP12.1, U40.11 (3Y); also elsewhere on the board
/ENCODER_CONN_A/ENC.Z: TP18.1, U39.11 (3Y); also elsewhere on the board
/ENCODER_CONN_A/ENC_PWR: C147.2, J13.19, U56.1 (VOUT); also elsewhere on the board
/ENCODER_CONN_A/ENC_SPI_MISO: D39.1 (IO1), D39.10 (NC), J13.10, R88.1, U41.10 (B1)
/ENCODER_CONN_A/ENC_SPI_MOSI: D39.4 (IO3), D39.7 (NC), J13.8, U41.8 (B3)
/ENCODER_CONN_A/ENC_SPI_NSS: D39.2 (IO2), D39.9 (NC), J13.9, U41.9 (B2)
/ENCODER_CONN_A/ENC_SPI_SCK: D39.5 (IO4), D39.6 (NC), J13.7, U41.7 (B4)
/ENCODER_CONN_A/HALL_U_N: J13.14, R82.1, U40.1 (1B)
/ENCODER_CONN_A/HALL_U_P: J13.13, R82.2, U40.2 (1A)
/ENCODER_CONN_A/HALL_V_N: J13.16, R83.1, U40.7 (2B)
/ENCODER_CONN_A/HALL_V_P: J13.15, R83.2, U40.6 (2A)
/ENCODER_CONN_A/HALL_W_N: J13.18, R84.1, U40.9 (3B)
/ENCODER_CONN_A/HALL_W_P: J13.17, R84.2, U40.10 (3A)
/ENCODER_CONN_A/MOTOT_TMP_N: C80.2, J13.12, NT21.2
/ENCODER_CONN_A/Z_N: J13.6, R81.1, U39.9 (3B)
/ENCODER_CONN_A/Z_P: J13.5, R81.2, U39.10 (3A)
/MA_TEMP: C80.1, J13.11, R85.2; also elsewhere on the board
GND: C79.2, C81.2, C82.2, C83.2, C145.2, C147.1, D39.3 (GND), D39.8 (NC), J13.20, NT21.1, R86.1, U39.8 (GND), U39.12 (~EN), U40.8 (GND), U40.12 (~EN), U41.6 (GND), U56.2 (GND); also elsewhere on the board
unnamed: R86.2, U56.3 (SET)

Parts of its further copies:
C84, C86, C87, C88, C146, C148: 100nF,16V; C_0402_1005Metric
C85: 1uF,25V; C_0402_1005Metric
D40: RCLAMP0524P; Diodes_UDFN-10_1.0x2.5mm_P0.5mm
J14: PHB2.0-02-20PWZ
NT22: NetTie_2; NetTie_SMD_5mil
R87, R98: 10K,1%; R_0402_1005Metric
R89, R90, R91, R92, R93, R94: 100R,1%,250mW; R_0603_1608Metric
R95: 1K,1%; R_0402_1005Metric
TP2, TP5, TP7, TP9, TP11, TP13, TP15, TP17, TP19, TP37: test_point_0.5mm
U42, U43: MS2575T; TSSOP-16_4.4x5mm_P0.65mm
U44: TXB0104RUTR; UQFN-12_1.7x2_Pitch0.4mm
U57: MT9700; SOT-23-5

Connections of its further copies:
+3.3V: C84.1, C86.1, C87.1, R95.1, U42.4 (EN), U42.16 (VCC), U43.4 (EN), U43.16 (VCC), U44.1 (VCCA), U44.12 (OE); also elsewhere on the board
+5V: C88.1, C146.1, R98.2, U44.11 (VCCB), U57.5 (VIN); also elsewhere on the board
/ENCODER_CONN_B/A_N: J14.2, R89.1, U42.1 (1B)
/ENCODER_CONN_B/A_P: J14.1, R89.2, U42.2 (1A)
/ENCODER_CONN_B/B_N: J14.4, R90.1, U42.7 (2B)
/ENCODER_CONN_B/B_P: J14.3, R90.2, U42.6 (2A)
/ENCODER_CONN_B/ENC.A: TP15.1, U42.3 (1Y); also elsewhere on the board
/ENCODER_CONN_B/ENC.B: TP17.1, U42.5 (2Y); also elsewhere on the board
/ENCODER_CONN_B/ENC.CLK: TP37.1, U44.5 (A4); also elsewhere on the board
/ENCODER_CONN_B/ENC.CS: TP5.1, U44.3 (A2); also elsewhere on the board
/ENCODER_CONN_B/ENC.MISO: TP7.1, U44.2 (A1); also elsewhere on the board
/ENCODER_CONN_B/ENC.MOSI: TP2.1, U44.4 (A3); also elsewhere on the board
/ENCODER_CONN_B/ENC.PWR: U57.4 (EN); also elsewhere on the board
/ENCODER_CONN_B/ENC.U: TP9.1, U43.3 (1Y); also elsewhere on the board
/ENCODER_CONN_B/ENC.V: TP11.1, U43.5 (2Y); also elsewhere on the board
/ENCODER_CONN_B/ENC.W: TP13.1, U43.11 (3Y); also elsewhere on the board
/ENCODER_CONN_B/ENC.Z: TP19.1, U42.11 (3Y); also elsewhere on the board
/ENCODER_CONN_B/ENC_PWR: C148.2, J14.19, U57.1 (VOUT); also elsewhere on the board
/ENCODER_CONN_B/ENC_SPI_MISO: D40.1 (IO1), D40.10 (NC), J14.10, R98.1, U44.10 (B1)
/ENCODER_CONN_B/ENC_SPI_MOSI: D40.4 (IO3), D40.7 (NC), J14.8, U44.8 (B3)
/ENCODER_CONN_B/ENC_SPI_NSS: D40.2 (IO2), D40.9 (NC), J14.9, U44.9 (B2)
/ENCODER_CONN_B/ENC_SPI_SCK: D40.5 (IO4), D40.6 (NC), J14.7, U44.7 (B4)
/ENCODER_CONN_B/HALL_U_N: J14.14, R92.1, U43.1 (1B)
/ENCODER_CONN_B/HALL_U_P: J14.13, R92.2, U43.2 (1A)
/ENCODER_CONN_B/HALL_V_N: J14.16, R93.1, U43.7 (2B)
/ENCODER_CONN_B/HALL_V_P: J14.15, R93.2, U43.6 (2A)
/ENCODER_CONN_B/HALL_W_N: J14.18, R94.1, U43.9 (3B)
/ENCODER_CONN_B/HALL_W_P: J14.17, R94.2, U43.10 (3A)
/ENCODER_CONN_B/MOTOT_TMP_N: C85.2, J14.12, NT22.2
/ENCODER_CONN_B/Z_N: J14.6, R91.1, U42.9 (3B)
/ENCODER_CONN_B/Z_P: J14.5, R91.2, U42.10 (3A)
/MB_TEMP: C85.1, J14.11, R95.2; also elsewhere on the board
GND: C84.2, C86.2, C87.2, C88.2, C146.2, C148.1, D40.3 (GND), D40.8 (NC), J14.20, NT22.1, R87.1, U42.8 (GND), U42.12 (~EN), U43.8 (GND), U43.12 (~EN), U44.6 (GND), U57.2 (GND); also elsewhere on the board
unnamed: R87.2, U57.3 (SET)

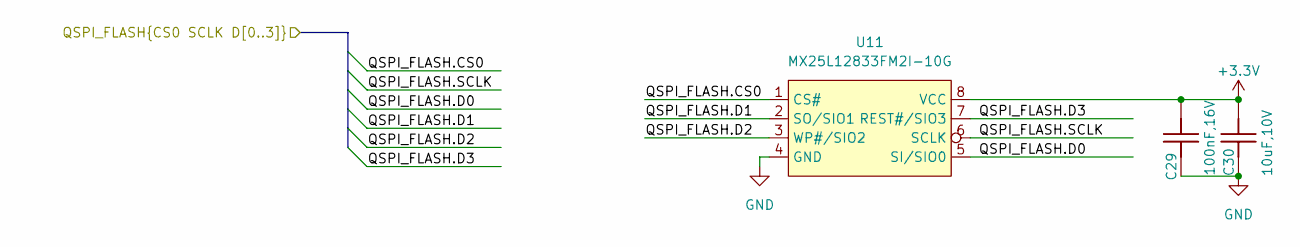
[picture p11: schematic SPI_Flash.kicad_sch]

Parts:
C29: 100nF,16V; C_0402_1005Metric
C30: 10uF,10V; C_0402_1005Metric
U11: MX25L12833FM2I-10G; SOIC-8_5.3x5.3mm_P1.27mm

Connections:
+3.3V: C29.1, C30.1, U11.8 (VCC); also elsewhere on the board
/HPM5E31_TOP/FLASH.CS0: U11.1 (CS#); also elsewhere on the board
/HPM5E31_TOP/FLASH.D0: U11.5 (SI/SIO0); also elsewhere on the board
/HPM5E31_TOP/FLASH.D1: U11.2 (SO/SIO1); also elsewhere on the board
/HPM5E31_TOP/FLASH.D2: U11.3 (WP#/SIO2); also elsewhere on the board
/HPM5E31_TOP/FLASH.D3: U11.7 (REST#/SIO3); also elsewhere on the board
/HPM5E31_TOP/FLASH.SCLK: U11.6 (SCLK); also elsewhere on the board
GND: C29.2, C30.2, U11.4 (GND); also elsewhere on the board

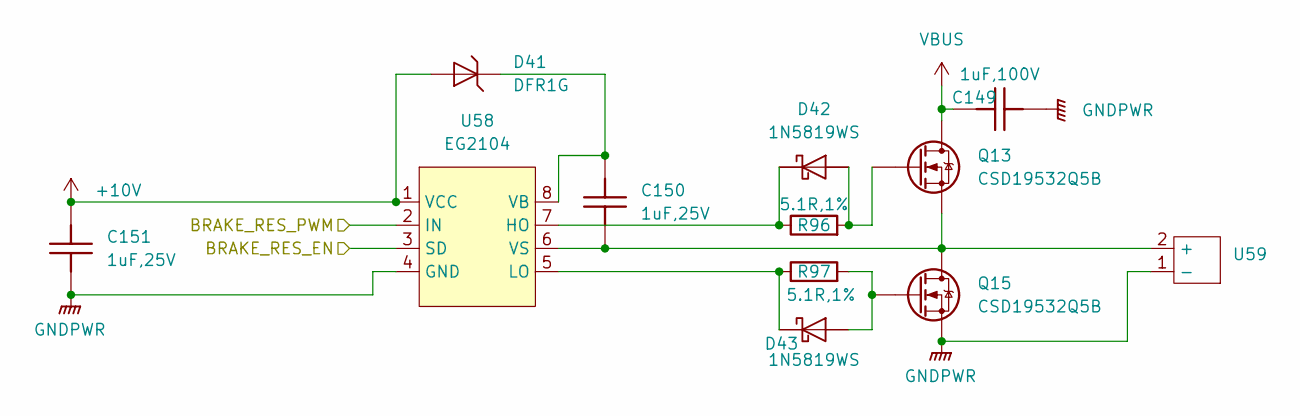
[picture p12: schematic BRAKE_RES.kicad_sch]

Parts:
C149: 1uF,100V; C_1206_3216Metric
C150, C151: 1uF,25V; C_0402_1005Metric
D41: DFR1G; D_SOD-123
D42, D43: 1N5819WS; D_SOD-323
Q13, Q15: CSD19532Q5B; PQFN-8-EP_6x5mm_P1.27mm_Generic
R96, R97: 5.1R,1%; R_0402_1005Metric
U58: EG2104; SOP-8_3.9x4.9mm_P1.27mm
U59: AMASS_XT30UPB-M_1x02_P5.0mm_Vertical

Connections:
+10V: C151.1, D41.2 (A), U58.1 (VCC); also elsewhere on the board
/BRAKE_RES/BRAKE_RES_EN: U58.3 (SD); also elsewhere on the board
GNDPWR: C149.2, C151.2, Q15.3 (S), U58.4 (GND), U59.1 (-); also elsewhere on the board
unnamed: C150.1, D41.1 (K), U58.8 (VB)
unnamed: D42.2 (A), Q13.2 (G), R96.2
unnamed: D42.1 (K), R96.1, U58.7 (HO)
unnamed: D43.2 (A), Q15.2 (G), R97.2
unnamed: D43.1 (K), R97.1, U58.5 (LO)
unnamed: C150.2, Q13.3 (S), Q15.1 (D), U58.6 (VS), U59.2 (+)
PE2: U58.2 (IN); also elsewhere on the board
VBUS: C149.1, Q13.1 (D); also elsewhere on the board

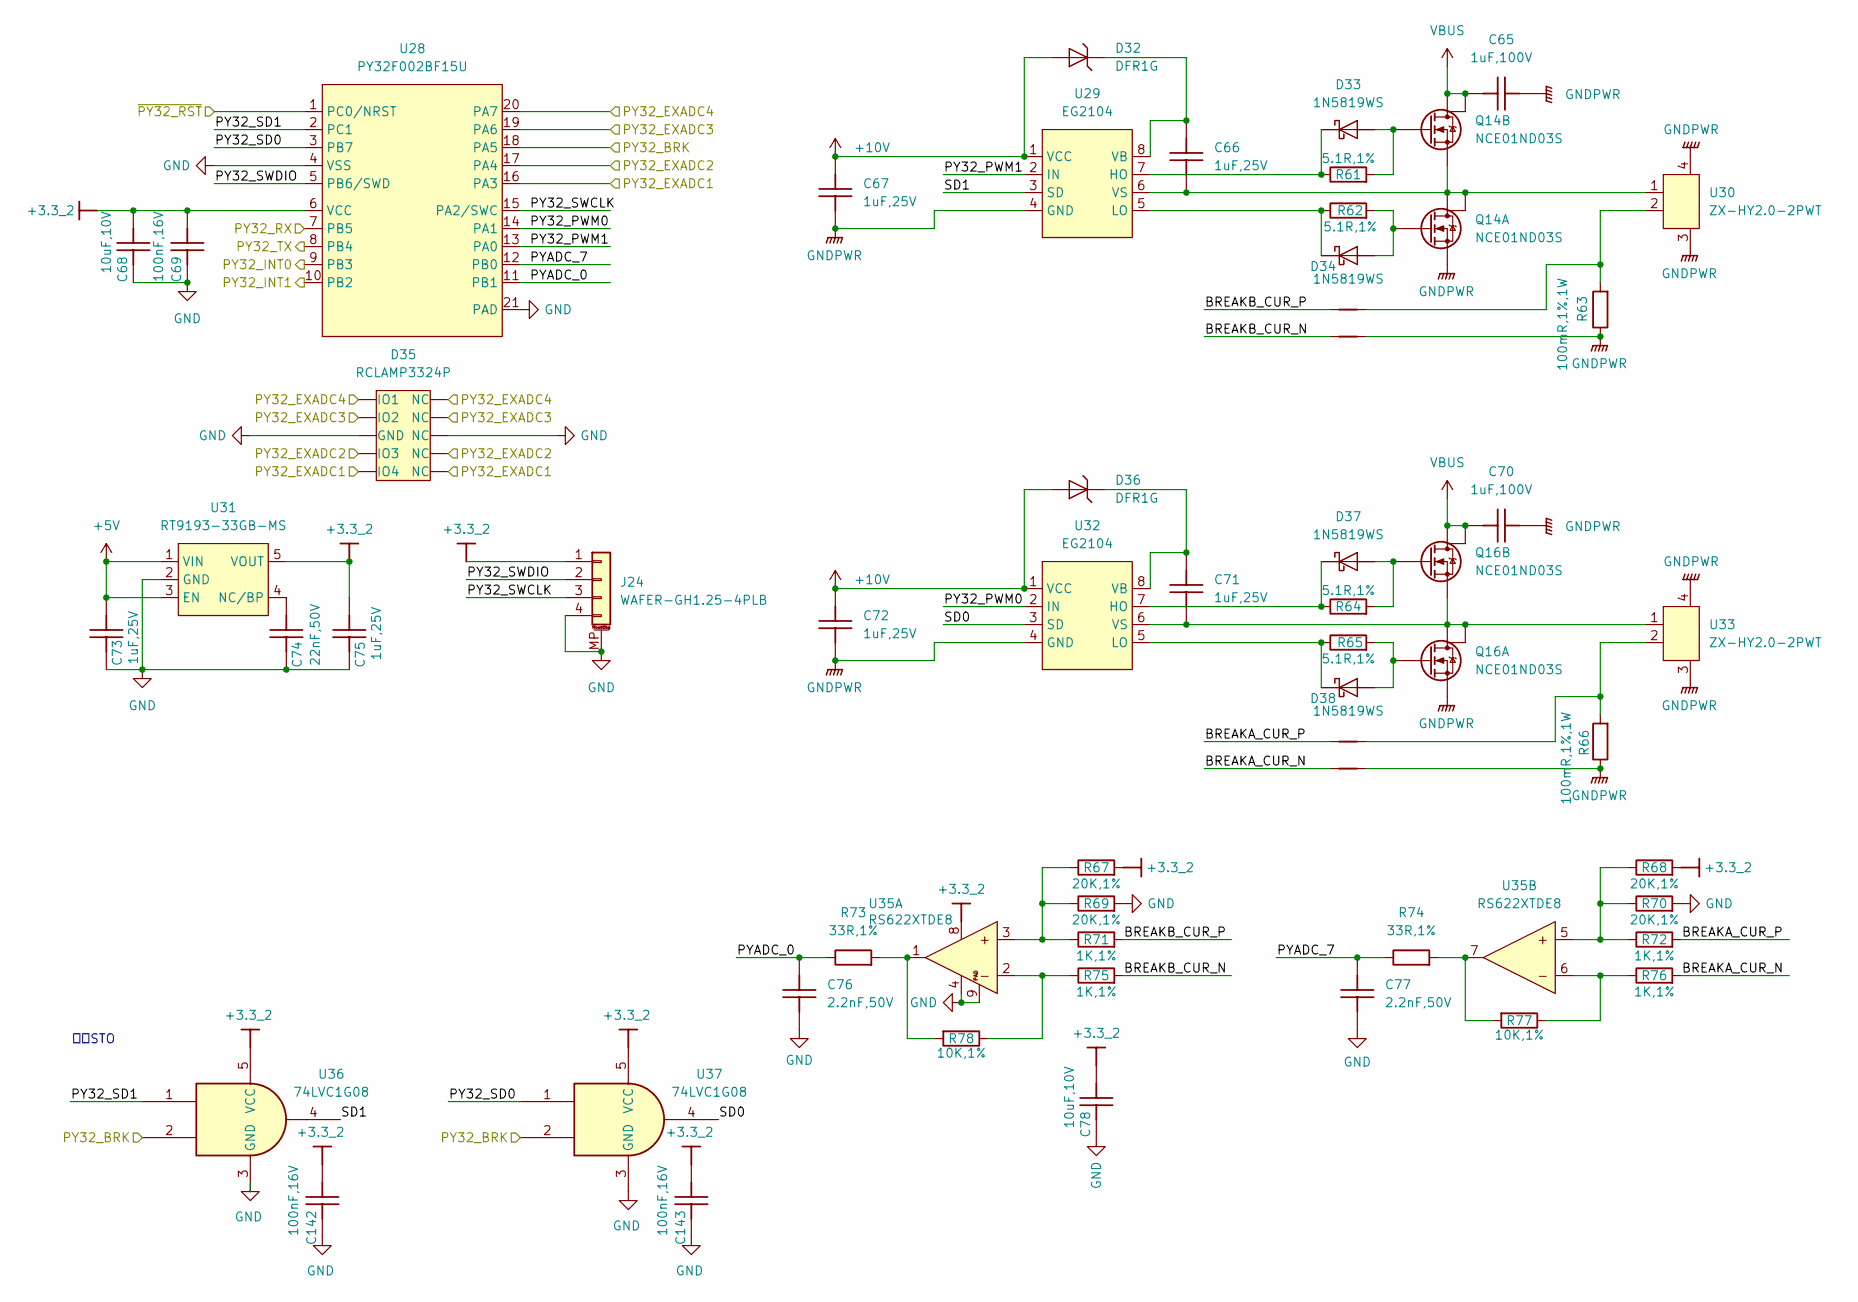
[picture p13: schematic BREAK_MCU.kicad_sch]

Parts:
C65, C70: 1uF,100V; C_1206_3216Metric
C66, C67, C71, C72, C73, C75: 1uF,25V; C_0402_1005Metric
C68, C78: 10uF,10V; C_0402_1005Metric
C69, C142, C143: 100nF,16V; C_0402_1005Metric
C74: 22nF,50V; C_0402_1005Metric
C76, C77: 2.2nF,50V; C_0402_1005Metric
D32, D36: DFR1G; D_SOD-123
D33, D34, D37, D38: 1N5819WS; D_SOD-323
D35: RCLAMP3324P; Diodes_UDFN-10_1.0x2.5mm_P0.5mm
J24: WAFER-GH1.25-4PLB; JST_SH_BM04B-SRSS-TB_1x04-1MP_P1.00mm_Vertical
NT17, NT18, NT19, NT20: NetTie_2; NetTie_SMD_5mil
Q14, Q16: NCE01ND03S; SOP-8_3.9x4.9mm_P1.27mm
R61, R62, R64, R65: 5.1R,1%; R_0402_1005Metric
R63, R66: 100mR,1%,1W; R_1206_3216Metric
R67, R68, R69, R70: 20K,1%; R_0402_1005Metric
R71, R72, R75, R76: 1K,1%; R_0402_1005Metric
R73, R74: 33R,1%; R_0402_1005Metric
R77, R78: 10K,1%; R_0402_1005Metric
U28: PY32F002BF15U; QFN-20-1EP_3x3mm_P0.4mm_EP1.65x1.65mm
U29, U32: EG2104; SOP-8_3.9x4.9mm_P1.27mm
U30, U33: ZX-HY2.0-2PWT
U31: RT9193-33GB-MS; SOT-23-5
U35: RS622XTDE8; DFN-8-1EP_2x2mm_P0.5mm_EP0.6x1.2mm
U36, U37: 74LVC1G08; SOT-353_SC-70-5

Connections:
+3.3_2: C68.2, C69.1, C75.1, C78.2, C142.1, C143.1, J24.1, R67.2, R68.2, U28.6 (VCC), U31.5 (VOUT), U35.8 (V+), U36.5 (VCC), U37.5 (VCC); also elsewhere on the board
+5V: C73.1, U31.1 (VIN), U31.3 (EN); also elsewhere on the board
+10V: C67.1, C72.1, D32.2 (A), D36.2 (A), U29.1 (VCC), U32.1 (VCC); also elsewhere on the board
/BREAK_MCU/BREAKA_CUR_N: NT20.1, R76.2
/BREAK_MCU/BREAKA_CUR_P: NT19.1, R72.2
/BREAK_MCU/BREAKB_CUR_N: NT18.1, R75.2
/BREAK_MCU/BREAKB_CUR_P: NT17.1, R71.2
/BREAK_MCU/PY32_EXADC3: D35.2 (IO2), D35.9 (NC), U28.19 (PA6)
/BREAK_MCU/PY32_EXADC4: D35.1 (IO1), D35.10 (NC), U28.20 (PA7)
/BREAK_MCU/PY32_PWM0: U28.14 (PA1), U32.2 (IN)
/BREAK_MCU/PY32_PWM1: U28.13 (PA0), U29.2 (IN)
/BREAK_MCU/PY32_SD0: U28.3 (PB7), U37.1
/BREAK_MCU/PY32_SD1: U28.2 (PC1), U36.1
/BREAK_MCU/PY32_SWCLK: J24.3, U28.15 (PA2/SWC)
/BREAK_MCU/PY32_SWDIO: J24.2, U28.5 (PB6/SWD)
/BREAK_MCU/PYADC_0: C76.1, R73.1, U28.11 (PB1)
/BREAK_MCU/PYADC_7: C77.1, R74.1, U28.12 (PB0)
/BREAK_MCU/SD0: U32.3 (SD), U37.4
/BREAK_MCU/SD1: U29.3 (SD), U36.4
/MA_TEMP: D35.4 (IO3), D35.7 (NC), U28.17 (PA4); also elsewhere on the board
/MB_TEMP: D35.5 (IO4), D35.6 (NC), U28.16 (PA3); also elsewhere on the board
/nBREAK: U28.18 (PA5), U36.2, U37.2; also elsewhere on the board
GND: C68.1, C69.2, C73.2, C74.2, C75.2, C76.2, C77.2, C78.1, C142.2, C143.2, D35.3 (GND), D35.8 (NC), J24.4, J24.MP (MountPin), R69.2, R70.2, U28.4 (VSS), U28.21 (PAD), U31.2 (GND), U35.4 (V-), U35.9 (PAD), U36.3 (GND), U37.3 (GND); also elsewhere on the board
GNDPWR: C65.1, C67.2, C70.1, C72.2, NT18.2, NT20.2, Q14.3 (S1), Q16.3 (S1), R63.1, R66.1, U29.4 (GND), U30.3 (PAD), U30.4 (PAD), U32.4 (GND), U33.3 (PAD), U33.4 (PAD); also elsewhere on the board
unnamed: C66.1, D32.1 (K), U29.8 (VB)
unnamed: D33.2 (A), Q14.2 (G2), R61.2
unnamed: D33.1 (K), R61.1, U29.7 (HO)
unnamed: D34.2 (A), Q14.4 (G1), R62.2
unnamed: D34.1 (K), R62.1, U29.5 (LO)
unnamed: C71.1, D36.1 (K), U32.8 (VB)
unnamed: D37.2 (A), Q16.2 (G2), R64.2
unnamed: D37.1 (K), R64.1, U32.7 (HO)
unnamed: D38.2 (A), Q16.4 (G1), R65.2
unnamed: D38.1 (K), R65.1, U32.5 (LO)
unnamed: NT17.2, R63.2, U30.2
unnamed: NT19.2, R66.2, U33.2
unnamed: C66.2, Q14.1 (S2), Q14.5 (D1), Q14.6 (D1), U29.6 (VS), U30.1
unnamed: C71.2, Q16.1 (S2), Q16.5 (D1), Q16.6 (D1), U32.6 (VS), U33.1
unnamed: C74.1, U31.4 (NC/BP)
unnamed: R67.1, R69.1, R71.1, U35.3 (+INB)
unnamed: R75.1, R78.1, U35.2 (-INB)
unnamed: R73.2, R78.2, U35.1 (OUTB)
unnamed: R68.1, R70.1, R72.1, U35.5 (+INB)
unnamed: R76.1, R77.1, U35.6 (-INB)
unnamed: R74.2, R77.2, U35.7 (OUTB)
PC8: U28.7 (PB5); also elsewhere on the board
PC9: U28.8 (PB4); also elsewhere on the board
PC11: U28.9 (PB3); also elsewhere on the board
PC12: U28.10 (PB2); also elsewhere on the board
PF29: U28.1 (PC0/NRST); also elsewhere on the board
VBUS: C65.2, C70.2, Q14.7 (D2), Q14.8 (D2), Q16.7 (D2), Q16.8 (D2); also elsewhere on the board

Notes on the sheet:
硬件STO

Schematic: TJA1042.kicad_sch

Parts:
C110, C111: 47pF,50V; C_0402_1005Metric
C112, C113: 100nF,16V; C_0402_1005Metric
J20: WAFER-GH1.25-2PWB; JST_GH_SM02B-GHS-TB_1x02-1MP_P1.25mm_Horizontal
L8: SDCW2012-2-102TF; L_CommonModeChoke_Coilcraft_0805USB
R126: 120R,1%; R_0603_1608Metric
TP33, TP35: test_point_0.5mm
U52: TJA1042TK/3; VSON-8-1EP_3x3mm_P0.65mm_EP1.6x2.4mm

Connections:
+3.3V: C113.1, U52.5 (VIO); also elsewhere on the board
+5V: C112.1, U52.3 (VCC); also elsewhere on the board
/HPM5E31_TOP/CAN3.RXD: TP35.1, U52.4 (RXD); also elsewhere on the board
/HPM5E31_TOP/CAN3.TXD: TP33.1, U52.1 (TXD); also elsewhere on the board
GND: C110.1, C111.2, C112.2, C113.2, J20.MP (MountPin), U52.2 (GND), U52.8 (STB), U52.9 (EP); also elsewhere on the board
unnamed: C111.1, J20.1, L8.2, R126.1
unnamed: C110.2, J20.2, L8.3, R126.2
unnamed: L8.4, U52.7 (CAN_H)
unnamed: L8.1, U52.6 (CAN_L)

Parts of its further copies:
C114, C115: 47pF,50V; C_0402_1005Metric
C116, C117: 100nF,16V; C_0402_1005Metric
J21: WAFER-GH1.25-2PWB; JST_GH_SM02B-GHS-TB_1x02-1MP_P1.25mm_Horizontal
L9: SDCW2012-2-102TF; L_CommonModeChoke_Coilcraft_0805USB
R127: 120R,1%; R_0603_1608Metric
TP34, TP36: test_point_0.5mm
U53: TJA1042TK/3; VSON-8-1EP_3x3mm_P0.65mm_EP1.6x2.4mm

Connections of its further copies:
+3.3V: C117.1, U53.5 (VIO); also elsewhere on the board
+5V: C116.1, U53.3 (VCC); also elsewhere on the board
/HPM5E31_TOP/CAN0.RXD: TP36.1, U53.4 (RXD); also elsewhere on the board
/HPM5E31_TOP/CAN0.TXD: TP34.1, U53.1 (TXD); also elsewhere on the board
GND: C114.1, C115.2, C116.2, C117.2, J21.MP (MountPin), U53.2 (GND), U53.8 (STB), U53.9 (EP); also elsewhere on the board
unnamed: C115.1, J21.1, L9.2, R127.1
unnamed: C114.2, J21.2, L9.3, R127.2
unnamed: L9.4, U53.7 (CAN_H)
unnamed: L9.1, U53.6 (CAN_L)

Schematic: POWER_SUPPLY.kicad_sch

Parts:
C9: 10uF,100V; CP_Radial_D5.0mm_P2.50mm
C10, C13, C27: 2.2nF,50V; C_0402_1005Metric
C11, C14, C17, C20: 10uF,10V; C_0402_1005Metric
C12: 47pF,50V; C_0402_1005Metric
C15: 100nF,50V; C_0603_1608Metric
C16, C18, C19: 22uF,25V; C_0805_2012Metric
C21, C22, C25, C26: 100nF,10V; C_0201_0603Metric
C23, C24: 1uF,25V; C_0402_1005Metric
C28: 100nF,16V; C_0402_1005Metric
C154: 4.7uF,25V; C_0805_2012Metric
D11: SMBJ54A; D_SMB
F1: JFC2410-1100TS; JFC2410
FB1, FB2: 600Ω@100MHz; L_0402_1005Metric
L1: 100uH,490mA; L_Changjiang_FNR4030S
L2: 1uH,5.6A; L_Changjiang_FNR252012S
L3: 22uH,540mA; L_1008_2520Metric
L4: 4.7uH,2.4A; L_Changjiang_FNR252012S
R14, R20: 10K,1%; R_0402_1005Metric
R15: 365K,1%; R_0402_1005Metric
R16, R18, R49, R54: 50K,1%; R_0402_1005Metric
R17, R23: 200K,0.5%; R_0201_0603Metric
R19: 178K,0.5%; R_0201_0603Metric
R22: 2.1k,1%; R_0402_1005Metric
R24: 11K,1%; R_0402_1005Metric
R25: 44.2K,0.5%; R_0201_0603Metric
R26: 0R,1%; R_0805_2012Metric
R27: 100K,1%; R_0402_1005Metric
R32: 33R,1%; R_0402_1005Metric
R37, R44: 1K,1%; R_0402_1005Metric
R137: 140K,1%; R_0402_1005Metric
R138: 20K,1%; R_0402_1005Metric
U4: LM5164DDAR; HSOP-8-1EP_3.9x4.9mm_P1.27mm_EP2.41x3.1mm
U5, U8: MP1605GTF-Z; SOT-563
U6: AMASS_XT60-M_1x02_P7.20mm_Vertical
U7: JW5026; SOT-23-6
U9: LP5907MFX-3.3/NOPB; SOT-23-5
U10: REF3030AIDBZR; SOT-23-3
U61: RS621PXF; SOT-23-5

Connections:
+1V2: C14.1, L2.2, R17.2, U5.6 (OUT); also elsewhere on the board
+3.3V: C20.1, L4.2, R14.1, R23.2, U8.6 (OUT); also elsewhere on the board
+5V: C11.1, C17.1, C18.1, C19.1, C21.1, FB1.1, L3.2, R24.2, U5.3 (VIN), U8.3 (VIN), U8.5 (EN); also elsewhere on the board
+5VA: C22.1, C23.1, C25.1, FB1.2, U9.1 (IN), U9.3 (EN), U10.1 (IN)
+10V: C13.2, C16.1, C154.1, L1.2, R15.1, R20.1, U7.5 (VIN); also elsewhere on the board
/POWER_SUPPLY/FB: C12.2, R15.2, R18.1, U4.5 (FB)
/POWER_SUPPLY/PG10V: R20.2, U4.6 (PGOOD), U7.4 (EN)
/POWER_SUPPLY/VBUS_F: C9.1, F1.2, R49.2, R137.2, U4.2 (VIN)
/POWER_SUPPLY/VBUS_SW: C10.2, L1.1, R27.1, U4.8 (SW)
GND: C11.2, C14.2, C16.2, C17.2, C18.2, C19.2, C20.2, C21.2, FB2.1, R19.1, R22.1, R25.2, R26.2, U5.2 (GND), U7.2 (GND), U8.2 (GND); also elsewhere on the board
GNDA: C22.2, C23.2, C24.2, C25.2, C26.2, C27.2, C28.2, FB2.2, R44.1, U9.2 (GND), U10.3 (GND), U61.2 (V-); also elsewhere on the board
GNDPWR: C9.2, C154.2, D11.2 (A), R16.2, R18.2, R26.1, R54.2, R138.1, U4.1 (GND), U4.9 (EP), U6.1 (-); also elsewhere on the board
unnamed: C12.1, C13.1, R27.2
unnamed: C10.1, U4.7 (BST)
unnamed: R137.1, R138.2, U4.3 (EN/UVLO)
unnamed: R16.1, U4.4 (RON)
unnamed: R14.2, U5.5 (EN)
unnamed: R17.1, R19.2, U5.1 (FB)
unnamed: L2.1, U5.4 (SW)
unnamed: C15.2, U7.1 (BST)
unnamed: R22.2, R24.1, U7.3 (FB)
unnamed: C15.1, L3.1, U7.6 (SW)
unnamed: R23.1, R25.1, U8.1 (FB)
unnamed: L4.1, U8.4 (SW)
unnamed: R44.2, R49.1, U61.3 (+IN)
unnamed: R37.2, R54.1, U61.4 (-IN)
unnamed: R32.1, R37.1, U61.1 (OUT)
PF27: C27.1, R32.2; also elsewhere on the board
VBUS: D11.1 (K), F1.1, U6.2 (+); also elsewhere on the board
VDDA: C24.1, C28.1, U9.5 (OUT), U61.5 (V+); also elsewhere on the board
VREF: C26.1, U10.2 (OUT); also elsewhere on the board

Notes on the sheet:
10V低压主电源
输入插座
MCU内核1.274V电源 1.27V [1.25V ... 1.29V]
RON_K = Vout * 2500 / Fsw_Khz = 10 * 2500 / 500 = 50
模拟供电&电压基准
UVLO 12V
系统3.3V电源 3.31V [3.26V ... 3.38V]
系统5V电源
母线电压采集

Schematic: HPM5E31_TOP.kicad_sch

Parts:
D1, D2: RCLAMP3324P; Diodes_UDFN-10_1.0x2.5mm_P0.5mm
D3: NCD0603G1; LED_0603_1608Metric
D4: NCD0603R1; LED_0603_1608Metric
D5: NCD0603B1; LED_0603_1608Metric
J1, J2: Conn_Coaxial; SMA_BAT_Wireless_BWSMA-KWE-Z001
J3: WAFER-ZH1.5-4PWB; ZH_SM04_1.50mm_Horizontal
J4: Conn_02x05_Odd_Even; IDC_SMD_P1.27mm_02x05
K1: DSHP02TSGET; SW_DIP_SPSTx02_Slide_KingTek_DSHP02TS_W7.62mm_P1.27mm
R1, R2, R6, R7, R8: 2K,1%; R_0402_1005Metric
R3, R4, R5, R134, R146, R184, R185: 10K,1%; R_0402_1005Metric

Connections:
+3.3V: J3.1, J4.1, K1.1 (PIN1), K1.2 (PIN2), R3.2, R4.2, R6.2, R7.2, R8.2, R134.2, R146.2, R184.2, R185.2; also elsewhere on the board
/HPM5E31_TOP/~RESET: D1.2 (IO2), D1.9 (NC), J4.10; also elsewhere on the board
GND: D1.3 (GND), D1.8 (NC), D2.3 (GND), D2.8 (NC), J1.2 (Ext), J2.2 (Ext), J3.4, J3.MP (MountPin), J4.3, J4.5, R5.2; also elsewhere on the board
unnamed: D3.2 (A), R6.1
unnamed: D4.2 (A), R7.1
unnamed: D5.2 (A), R8.1
unnamed: K1.3 (PIN3), R2.1
unnamed: K1.4 (PIN4), R1.1
PA0: D1.4 (IO3), D1.7 (NC), J3.3; also elsewhere on the board
PA1: D1.1 (IO1), D1.10 (NC), J3.2; also elsewhere on the board
PA2: R1.2; also elsewhere on the board
PA3: R2.2; also elsewhere on the board
PA4: D2.1 (IO1), D2.10 (NC), J4.6; also elsewhere on the board
PA5: D2.5 (IO4), D2.6 (NC), J4.8, R4.1; also elsewhere on the board
PA6: D2.4 (IO3), D2.7 (NC), J4.4, R5.1; also elsewhere on the board
PA7: D2.2 (IO2), D2.9 (NC), J4.2, R3.1; also elsewhere on the board
PA8: D1.5 (IO4), D1.6 (NC), J4.9, R134.1; also elsewhere on the board
PC2: D3.1 (K); also elsewhere on the board
PC3: D4.1 (K); also elsewhere on the board
PC11: R185.1; also elsewhere on the board
PC12: R184.1; also elsewhere on the board
PC18: D5.1 (K); also elsewhere on the board
PE4: J1.1 (In); also elsewhere on the board
PE5: J2.1 (In); also elsewhere on the board
PF29: R146.1; also elsewhere on the board

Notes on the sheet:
TRGM高速连接器
三色用户LED
UART0

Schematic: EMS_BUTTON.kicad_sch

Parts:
C141: 100nF,16V; C_0402_1005Metric
C155: 1uF,25V; C_0402_1005Metric
J23: WAFER-GH1.25-4PWB; JST_GH_SM04B-GHS-TB_1x04-1MP_P1.25mm_Horizontal
R131, R132, R133: 499,1%; R_0402_1005Metric
R136: 4.7K,1%; R_0402_1005Metric
R139: 0R,1%; R_0402_1005Metric
U54: TLP2362; SO-5-6_4.55x3.7mm_P1.27mm

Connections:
+3.3V: C141.1, R136.2, U54.6 (VCC); also elsewhere on the board
+5V: R131.2; also elsewhere on the board
/nBREAK: C155.1, R136.1, R139.2; also elsewhere on the board
GND: C141.2, C155.2, J23.MP (MountPin), R133.2, U54.4 (GND); also elsewhere on the board
unnamed: J23.1, R131.1
unnamed: J23.2, R132.1
unnamed: J23.3, U54.3
unnamed: J23.4, R133.1
unnamed: R132.2, U54.1
unnamed: R139.1, U54.5

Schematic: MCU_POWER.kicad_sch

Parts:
C118, C119, C120, C121, C124, C126, C128, C132, C134, C136, C139: 100nF,10V; C_0201_0603Metric
C122, C123, C125, C127, C131, C133, C137, C138: 10uF,10V; C_0402_1005Metric
C129, C130: 10pF,50V; C_0402_1005Metric
C135: 4.7uF,10V; C_0402_1005Metric
C140, C144: 100nF,16V; C_0402_1005Metric
FB3: 600Ω@100MHz; L_0402_1005Metric
J22: USB_B; USB_B_OST_USB-B1HSxx_Horizontal
R128, R129, R135: 10K,1%; R_0402_1005Metric
R130: 33R,1%; R_0402_1005Metric
U3: HPM5E31IGN1; BGA-196_14x14_12.0x12.0mm_P0.8mm
U55: ECMF02-2AMX6; ST_UQFN-6L_1.5x1.7mm_P0.5mm
X1: 24M,10ppm; Oscillator_SMD_Abracon_ASCO-4Pin_1.6x1.2mm

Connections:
+1V2: C118.1, C119.1, C120.1, C121.1, C122.1, C123.1, U3.F6 (VDD_SOC), U3.F9 (VDD_SOC), U3.G6 (VDD_SOC), U3.G9 (VDD_SOC), U3.H9 (VDD_SOC); also elsewhere on the board
+3.3V: C127.1, C128.1, R135.2, U3.N4 (VPMC), U3.P4 (VPMC); also elsewhere on the board
/HPM5E31_TOP/MCU_POWER/USB'_N: J22.2 (D-), U55.5 (D-)
/HPM5E31_TOP/MCU_POWER/USB'_P: J22.3 (D+), U55.6 (D+)
/HPM5E31_TOP/MCU_POWER/USB_N: U3.L13 (USB0_DN), U55.2 (D-)
/HPM5E31_TOP/MCU_POWER/USB_P: U3.L14 (USB0_DP), U55.1 (D+)
/HPM5E31_TOP/MCU_POWER/USB_VBUS: J22.1 (VBUS), R130.1
/HPM5E31_TOP/MCU_POWER/VANA: C124.1, C125.1, FB3.2, U3.J9 (VANA)
/HPM5E31_TOP/MCU_POWER/VDD_OTPCAP: C135.1, C136.1, U3.K8 (VDD_OTPCAP)
/HPM5E31_TOP/MCU_POWER/VDD_PHY0CAP: C133.1, C134.1, U3.J6 (VDD_PHY0CAP)
/HPM5E31_TOP/MCU_POWER/VDD_PHY1CAP: C131.1, C132.1, U3.H6 (VDD_PHY1CAP)
/HPM5E31_TOP/MCU_POWER/VDD_PMCCAP: C137.1, C138.1, C139.1, U3.K7 (VDD_PMCCAP)
/HPM5E31_TOP/MCU_POWER/XTALI: C130.1, U3.K14 (XTALI), X1.1 (X1)
/HPM5E31_TOP/MCU_POWER/XTALO: C129.2, U3.K13 (XTALO), X1.3 (X2)
/HPM5E31_TOP/~RESET: C144.1, R135.1, U3.M3 (RSTN); also elsewhere on the board
GND: C118.2, C119.2, C120.2, C121.2, C122.2, C123.2, C127.2, C128.2, C129.1, C130.2, C131.2, C132.2, C133.2, C134.2, C135.2, C136.2, C137.2, C138.2, C139.2, C140.2, C144.2, J22.4 (GND), J22.5 (Shield), R128.1, R129.1, U3.A1 (VSS), U3.A14 (VSS), U3.E5 (VSS), U3.E10 (VSS), U3.F7 (VSS), U3.F8 (VSS), U3.G7 (VSS), U3.G8 (VSS), U3.H7 (VSS), U3.J7 (VSS), U3.K5 (VSS), U3.K10 (VSS), U3.N1 (DCDC_GND), U3.N3 (VSS), U3.P1 (VSS), U3.P2 (DCDC_GND), U3.P14 (VSS), U55.3 (GND), X1.2 (GND), X1.4 (GND); also elsewhere on the board
GNDA: C124.2, C125.2, C126.2, U3.H8 (VSSA), U3.J8 (VREFL); also elsewhere on the board
unnamed: R128.2, U3.M1 (DCDC_IN), U3.M2 (DCDC_IN)
unnamed: R129.2, U3.N2 (DCDC_LP), U3.P3 (DCDC_LP)
unnamed: C140.1, R130.2, U3.L12 (USB0_VBUS)
VDDA: FB3.1; also elsewhere on the board
VREF: C126.1, U3.K9 (VREFH); also elsewhere on the board

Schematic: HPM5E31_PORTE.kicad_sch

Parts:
U3: HPM5E31IGN1; BGA-196_14x14_12.0x12.0mm_P0.8mm

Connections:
/ETHERNET_PHY_P2/MII.LINK: U3.N14 (PE03/GPTMR1.CAPT1/UART0.CTS/I2C2.SDA/MC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); also elsewhere on the board
/HPM5E31_TOP/DRIVER_B.EN: U3.M14 (PE00/GPTMR1.COMP0/UART0.TXD/MCAN0.TXD/E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); also elsewhere on the board
PE1: U3.M13 (PE01/GPTMR1.CAPT0/UART0.RXD/MCAN0.RXD/E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)
PE2: U3.M12 (PE02/GPTMR1.COMP1/UART0.DE/UART0.RTS/I2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); also elsewhere on the board
PE4: U3.N13 (PE04/UART1.CTS/MCAN1.RXD/ESC0.CTR2/PWM0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); also elsewhere on the board
PE5: U3.P13 (PE05/GPTMR1.COMP2/UART1.DE/UART1.RTS/MC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); also elsewhere on the board

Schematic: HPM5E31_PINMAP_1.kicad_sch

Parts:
R9: 33R,1%; R_0201_0603Metric
R10, R11: 4.7K,1%; R_0402_1005Metric
TP20: test_point_0.5mm

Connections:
+3.3V: R10.1, R11.1; also elsewhere on the board
/ETHERNET_PHY_P2/MII.MDC: R11.2; also elsewhere on the board
/ETHERNET_PHY_P2/MII.MDIO: R10.2; also elsewhere on the board
/ETHERNET_PHY_P2/MII.REFCLK: R9.1; also elsewhere on the board
/ETHERNET_PHY_P2/MII.RST: TP20.1; also elsewhere on the board
PA9: R9.2; also elsewhere on the board

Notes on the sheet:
UART3
ADC_CH5
ADC_CH12
SPI2
CTR4
ADC_CH14
CTR5
CAN0
ADC_CH3
UART6
ADC_CH7
QEI1
CAN3
ADC_CH1
CTR1
ADC_CH11
QEI0
ADC_CH8
SPI3
SPI1
UART4

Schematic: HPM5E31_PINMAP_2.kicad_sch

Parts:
C1, C2, C3, C4: 100nF,16V; C_0402_1005Metric
D6, D7, D9: RCLAMP0524P; Diodes_UDFN-10_1.0x2.5mm_P0.5mm
D8: NCD0603G1; LED_0603_1608Metric
D10: NCD0603R1; LED_0603_1608Metric
J5: WAFER-GH1.25-6PWB; JST_GH_SM06B-GHS-TB_1x06-1MP_P1.25mm_Horizontal
J6: Conn_02x05_Odd_Even; IDC_SMD_P1.27mm_02x05
R12, R13: 2K,1%; R_0402_1005Metric
U1: TXS0108ERGYR; Texas_RGY_R-PVQFN-N20_EP2.05x3.05mm
U2: TXB0104RUTR; UQFN-12_1.7x2_Pitch0.4mm

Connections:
+3.3V: C1.1, C3.1, R12.2, R13.2, U1.2 (VCCA), U1.10 (OE), U2.1 (VCCA), U2.12 (OE); also elsewhere on the board
+5V: C2.1, C4.1, J5.5, J6.1, U1.19 (VCCB), U2.11 (VCCB); also elsewhere on the board
/HPM5E31_TOP/HPM5E31_PINMAP_2/ESC_GPIO_0: D7.1 (IO1), D7.10 (NC), J6.8, U1.18 (B2)
/HPM5E31_TOP/HPM5E31_PINMAP_2/ESC_GPIO_1: D7.2 (IO2), D7.9 (NC), J6.6, U1.17 (B3)
/HPM5E31_TOP/HPM5E31_PINMAP_2/ESC_GPIO_2: D7.4 (IO3), D7.7 (NC), J6.4, U1.16 (B4)
/HPM5E31_TOP/HPM5E31_PINMAP_2/ESC_GPIO_3: D9.1 (IO1), D9.10 (NC), J6.7, U1.15 (B5)
/HPM5E31_TOP/HPM5E31_PINMAP_2/ESC_GPIO_4: D9.2 (IO2), D9.9 (NC), J6.5, U1.14 (B6)
/HPM5E31_TOP/HPM5E31_PINMAP_2/ESC_GPIO_5: D9.4 (IO3), D9.7 (NC), J6.3, U1.13 (B7)
/HPM5E31_TOP/HPM5E31_PINMAP_2/EUI_CK: D6.4 (IO3), D6.7 (NC), J5.2, U2.8 (B3)
/HPM5E31_TOP/HPM5E31_PINMAP_2/EUI_DI: D6.1 (IO1), D6.10 (NC), J5.4, U2.10 (B1)
/HPM5E31_TOP/HPM5E31_PINMAP_2/EUI_DO: D6.2 (IO2), D6.9 (NC), J5.3, U2.9 (B2)
/HPM5E31_TOP/HPM5E31_PINMAP_2/EUI_SH: D6.5 (IO4), D6.6 (NC), J5.1, U2.7 (B4)
GND: C1.2, C2.2, C3.2, C4.2, D6.3 (GND), D6.8 (NC), D7.3 (GND), D7.8 (NC), D9.3 (GND), D9.8 (NC), J5.6, J5.MP (MountPin), J6.9, J6.10, U1.11 (GND), U1.21 (PAD), U2.6 (GND); also elsewhere on the board
unnamed: D8.2 (A), R12.1
unnamed: D10.2 (A), R13.1
PB26: U2.4 (A3); also elsewhere on the board
PB27: U2.5 (A4); also elsewhere on the board
PB28: U2.2 (A1); also elsewhere on the board
PB29: U2.3 (A2); also elsewhere on the board
PB30: D8.1 (K); also elsewhere on the board
PB31: D10.1 (K); also elsewhere on the board
PC17: U1.8 (A7); also elsewhere on the board
PD1: U1.7 (A6); also elsewhere on the board
PD2: U1.6 (A5); also elsewhere on the board
PD3: U1.5 (A4); also elsewhere on the board
PD4: U1.4 (A3); also elsewhere on the board
PD9: U1.3 (A2); also elsewhere on the board

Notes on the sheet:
EUI1
ESC错误LED
ESC_IO
ESC运行LED

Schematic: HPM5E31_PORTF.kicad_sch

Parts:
U3: HPM5E31IGN1; BGA-196_14x14_12.0x12.0mm_P0.8mm

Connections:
/HPM5E31_TOP/DRIVER_A.CUR0: U3.N5 (PF31/SDM0.CLK3/ADC0.IN07/ADC1.IN07/ACMP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); also elsewhere on the board
/HPM5E31_TOP/DRIVER_A.CUR1: U3.P5 (PF28/SDM0.DAT3/ADC0.IN05/ADC1.IN05/ACMP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); also elsewhere on the board
/HPM5E31_TOP/DRIVER_A.CUR2: U3.N6 (PF20/SDM0.DAT3/USB0.OC/ETH0.EVTO1/ESC0.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); also elsewhere on the board
/HPM5E31_TOP/DRIVER_A.CUR3: U3.P6 (PF26/SDM0.DAT1/ADC0.IN01/ADC1.IN01/ACMP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); also elsewhere on the board
/HPM5E31_TOP/DRIVER_A.EN: U3.P12 (PF06/I2C3.SDA/ESC0.P1_TXD3/PWM0.P6/TRGM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); also elsewhere on the board
/HPM5E31_TOP/DRIVER_A.HI0: U3.N10 (PF00/MCAN0.TXD/ESC0.MDC/PWM0.P0/TRGM.P0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); also elsewhere on the board
/HPM5E31_TOP/DRIVER_A.HI1: U3.P11 (PF02/I2C2.SCL/MCAN0.STBY/ESC0.P1_TXCK/P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); also elsewhere on the board
/HPM5E31_TOP/DRIVER_A.HI2: U3.M8 (PF04/MCAN1.RXD/ESC0.P1_TXD1/PWM0.P4/TRG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); also elsewhere on the board
/HPM5E31_TOP/DRIVER_A.LI0: U3.L10 (PF01/MCAN0.RXD/ESC0.MDIO/PWM0.P1/TRGM.P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); also elsewhere on the board
/HPM5E31_TOP/DRIVER_A.LI1: U3.M9 (PF03/I2C2.SDA/MCAN1.STBY/ESC0.P1_TXD0/P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); also elsewhere on the board
/HPM5E31_TOP/DRIVER_A.LI2: U3.L8 (PF05/MCAN1.TXD/ESC0.P1_TXD2/PWM0.P5/TRG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); also elsewhere on the board
/HPM5E31_TOP/DRIVER_B.CUR0: U3.P8 (PF18/SDM0.DAT1/USB0.PWR/ETH0.EVTO0/ESC0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); also elsewhere on the board
/HPM5E31_TOP/DRIVER_B.CUR1: U3.N8 (PF22/SDM0.CLK2/USB0.ID/ETH0.EVTI1/ESC0.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); also elsewhere on the board
/HPM5E31_TOP/DRIVER_B.CUR2: U3.P7 (PF17/SDM0.CLK0/ADC0.IN12/ADC1.IN12/ACMP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); also elsewhere on the board
/HPM5E31_TOP/DRIVER_B.CUR3: U3.N7 (PF16/SDM0.DAT0/ADC0.IN08/ADC1.IN08/ACMP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); also elsewhere on the board
/HPM5E31_TOP/DRIVER_B.HI0: U3.L11 (PF08/I2C0.SCL/MCAN2.TXD/ESC0.P1_RXDV/PW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); also elsewhere on the board
/HPM5E31_TOP/DRIVER_B.HI1: U3.P10 (PF10/MCAN2.STBY/ESC0.P1_RXD1/PWM1.P2/TR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); also elsewhere on the board
/HPM5E31_TOP/DRIVER_B.HI2: U3.N11 (PF12/I2C1.SDA/ESC0.P1_RXD3/PWM1.P4/TRGM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); also elsewhere on the board
/HPM5E31_TOP/DRIVER_B.LI0: U3.M10 (PF09/I2C0.SDA/MCAN2.RXD/ESC0.P1_RXD0/PW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); also elsewhere on the board
/HPM5E31_TOP/DRIVER_B.LI1: U3.L9 (PF11/ESC0.P1_RXD2/PWM1.P3/TRGM.P11/ETH0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); also elsewhere on the board
/HPM5E31_TOP/DRIVER_B.LI2: U3.N12 (PF13/I2C1.SCL/MCAN3.STBY/ESC0.P1_RXCK/P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); also elsewhere on the board
PF7: U3.M11 (PF07/I2C3.SCL/ESC0.P1_TXEN/PWM0.P7/TRGM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)
PF14: U3.N9 (PF14/MCAN3.RXD/ESC0.P1_RXER/PWM1.P6/TRG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)
PF15: U3.P9 (PF15/MCAN3.TXD/PWM1.P7/TRGM.P15/ETH0.TX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)
PF19: U3.M5 (PF19/SDM0.CLK1/USB0.PWR/ADC0.IN13/ADC1.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); also elsewhere on the board
PF21: U3.L6 (PF21/SDM0.DAT2/USB0.ID/ETH0.EVTI0/ESC0.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)
PF23: U3.L5 (PF23/SDM0.CLK3/USB0.OC/ADC0.IN15/ADC1.I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)
PF24: U3.M6 (PF24/SDM0.DAT0/ADC0.IN10/ADC1.IN10/ACMP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); also elsewhere on the board
PF25: U3.L7 (PF25/SDM0.CLK0/ADC0.IN09/ADC1.IN09/ACMP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)
PF27: U3.M7 (PF27/SDM0.CLK1/ADC0.IN00/ADC1.IN00/ACMP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); also elsewhere on the board
PF29: U3.M4 (PF29/SDM0.DAT2/ADC0.IN04/ADC1.IN04/ACMP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); also elsewhere on the board
PF30: U3.L4 (PF30/SDM0.CLK2/ADC0.IN06/ADC1.IN06/ACMP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)

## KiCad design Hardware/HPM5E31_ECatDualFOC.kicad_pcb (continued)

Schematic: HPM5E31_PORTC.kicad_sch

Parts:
U3: HPM5E31IGN1; BGA-196_14x14_12.0x12.0mm_P0.8mm

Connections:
/ENCODER_CONN_A/ENC.CLK: U3.B7 (PC04/UART1.CTS/SPI0.SCLK/MCAN1.RXD/ESC0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); also elsewhere on the board
/ENCODER_CONN_A/ENC.CS: U3.A8 (PC05/GPTMR1.COMP2/UART1.DE/UART1.RTS/SP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); also elsewhere on the board
/ENCODER_CONN_A/ENC.MISO: U3.B8 (PC06/GPTMR0.CAPT0/UART1.RXD/I2C3.SDA/SP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); also elsewhere on the board
/ENCODER_CONN_A/ENC.MOSI: U3.A9 (PC07/GPTMR0.COMP0/UART1.TXD/I2C3.SCL/SP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); also elsewhere on the board
/ENCODER_CONN_B/ENC.CLK: U3.A11 (PC20/UART5.CTS/SPI3.SCLK/ESC0.GPI43/ESC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); also elsewhere on the board
/ENCODER_CONN_B/ENC.CS: U3.B11 (PC21/GPTMR3.COMP2/UART5.DE/UART5.RTS/SP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); also elsewhere on the board
/ENCODER_CONN_B/ENC.MISO: U3.A12 (PC22/GPTMR2.CAPT0/UART5.RXD/SPI3.MISO/E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); also elsewhere on the board
/ENCODER_CONN_B/ENC.MOSI: U3.A13 (PC23/GPTMR2.COMP0/UART5.TXD/SPI3.MOSI/E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); also elsewhere on the board
/HPM5E31_TOP/CAN0.RXD: U3.A6 (PC01/GPTMR1.CAPT0/UART0.RXD/MCAN0.RXD/E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); also elsewhere on the board
/HPM5E31_TOP/CAN0.TXD: U3.B5 (PC00/GPTMR1.COMP0/UART0.TXD/MCAN0.TXD/E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); also elsewhere on the board
/HPM5E31_TOP/FLASH.CS0: U3.D13 (PC27/UART6.CTS/SPI2.CS0/ESC0.GPI36/ESC0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); also elsewhere on the board
/HPM5E31_TOP/FLASH.D0: U3.E13 (PC29/GPTMR3.COMP3/UART7.DE/UART7.RTS/SP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); also elsewhere on the board
/HPM5E31_TOP/FLASH.D1: U3.E14 (PC28/UART7.CTS/SPI2.MISO/ESC0.GPI35/ESC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); also elsewhere on the board
/HPM5E31_TOP/FLASH.D2: U3.F14 (PC30/UART7.RXD/SPI2.DAT2/ESC0.GPI33/ESC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); also elsewhere on the board
/HPM5E31_TOP/FLASH.D3: U3.F13 (PC31/GPTMR2.COMP3/UART7.TXD/SPI2.DAT3/E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); also elsewhere on the board
/HPM5E31_TOP/FLASH.SCLK: U3.D14 (PC26/GPTMR2.COMP2/UART6.DE/UART6.RTS/SP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); also elsewhere on the board
/HPM5E31_TOP/RS485_3.DE: U3.C7 (PC13/GPTMR1.COMP3/UART3.DE/UART3.RTS/I2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); also elsewhere on the board
/HPM5E31_TOP/RS485_3.DI: U3.C8 (PC15/GPTMR0.COMP3/UART3.TXD/SPI1.DAT3/M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); also elsewhere on the board
/HPM5E31_TOP/RS485_3.RO: U3.D7 (PC14/UART3.RXD/SPI1.DAT2/MCAN3.RXD/ESC0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); also elsewhere on the board
PC2: U3.B6 (PC02/GPTMR1.COMP1/UART0.DE/UART0.RTS/I2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); also elsewhere on the board
PC3: U3.A7 (PC03/GPTMR1.CAPT1/UART0.CTS/I2C2.SDA/SP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); also elsewhere on the board
PC8: U3.B9 (PC08/GPTMR0.COMP1/UART2.TXD/I2C0.SCL/SP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); also elsewhere on the board
PC9: U3.C5 (PC09/GPTMR0.CAPT1/UART2.RXD/I2C0.SDA/SP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); also elsewhere on the board
PC10: U3.D5 (PC10/GPTMR0.COMP2/UART2.DE/UART2.RTS/SP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); also elsewhere on the board
PC11: U3.C6 (PC11/UART2.CTS/SPI1.CS0/ESC0.GPI52/ESC0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); also elsewhere on the board
PC12: U3.D6 (PC12/UART3.CTS/I2C1.SDA/SPI1.MISO/ESC0.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); also elsewhere on the board
PC16: U3.D8 (PC16/GPTMR3.COMP0/UART4.TXD/ESC0.GPI47/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)
PC17: U3.C9 (PC17/GPTMR3.CAPT0/UART4.RXD/ESC0.GPI46/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); also elsewhere on the board
PC18: U3.A10 (PC18/GPTMR3.COMP1/UART4.DE/UART4.RTS/ES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); also elsewhere on the board
PC19: U3.B10 (PC19/GPTMR3.CAPT1/UART4.CTS/SPI2.CS3/ES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)
PC24: U3.B14 (PC24/GPTMR2.COMP1/UART6.TXD/SPI2.CS2/ES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)
PC25: U3.C14 (PC25/GPTMR2.CAPT1/UART6.RXD/SPI2.CS1/ES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)

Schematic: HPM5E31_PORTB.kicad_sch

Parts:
U3: HPM5E31IGN1; BGA-196_14x14_12.0x12.0mm_P0.8mm

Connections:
/ETHERNET_PHY_P0/MII.LINK: U3.B1 (PB25/ESC0.CTR5/XPI0.CA_DQS/SDM0.DAT3/ET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); also elsewhere on the board
/ETHERNET_PHY_P0/MII.RXC: U3.C2 (PB05/MCAN1.TXD/ESC0.P0_RXCK/PWM0.P5/TRG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); also elsewhere on the board
/ETHERNET_PHY_P0/MII.RXD0: U3.E2 (PB01/MCAN0.RXD/ESC0.P0_RXD0/PWM0.P1/TRG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); also elsewhere on the board
/ETHERNET_PHY_P0/MII.RXD1: U3.D1 (PB02/I2C2.SCL/MCAN0.STBY/ESC0.P0_RXD1/P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); also elsewhere on the board
/ETHERNET_PHY_P0/MII.RXD2: U3.D2 (PB03/I2C2.SDA/MCAN1.STBY/ESC0.P0_RXD2/P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); also elsewhere on the board
/ETHERNET_PHY_P0/MII.RXD3: U3.C1 (PB04/MCAN1.RXD/ESC0.P0_RXD3/PWM0.P4/TRG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); also elsewhere on the board
/ETHERNET_PHY_P0/MII.RX_DV: U3.E1 (PB00/MCAN0.TXD/ESC0.P0_RXDV/PWM0.P0/TRG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); also elsewhere on the board
/ETHERNET_PHY_P0/MII.TXC: U3.E3 (PB06/I2C3.SDA/ESC0.P0_TXCK/PWM0.P6/TRGM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); also elsewhere on the board
/ETHERNET_PHY_P0/MII.TXD0: U3.E4 (PB07/I2C3.SCL/ESC0.P0_TXD0/PWM0.P7/TRGM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); also elsewhere on the board
/ETHERNET_PHY_P0/MII.TXD1: U3.D3 (PB08/I2C0.SCL/MCAN2.TXD/ESC0.P0_TXD1/PW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); also elsewhere on the board
/ETHERNET_PHY_P0/MII.TXD2: U3.D4 (PB09/I2C0.SDA/MCAN2.RXD/ESC0.P0_TXD2/PW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); also elsewhere on the board
/ETHERNET_PHY_P0/MII.TXD3: U3.C3 (PB10/MCAN2.STBY/ESC0.P0_TXD3/PWM1.P2/TR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); also elsewhere on the board
/ETHERNET_PHY_P0/MII.TXEN: U3.C4 (PB11/ESC0.P0_TXEN/PWM1.P3/TRGM.P11/ETH0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); also elsewhere on the board
/ETHERNET_PHY_P2/MII.RST: U3.A2 (PB24/ESC0.CTR4/XPI0.CA_CS1/SDM0.CLK3/ET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); also elsewhere on the board
PB26: U3.A3 (PB26/ESC0.CTR6/XPI0.CA_D2/QEI1.H1/SDM0.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); also elsewhere on the board
PB27: U3.B2 (PB27/ESC0.CTR7/XPI0.CA_D0/QEI1.F/SDM0.D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); also elsewhere on the board
PB28: U3.A4 (PB28/ESC0.CTR8/XPI0.CA_D1/QEI1.H0/SDM0.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); also elsewhere on the board
PB29: U3.B3 (PB29/XPI0.CA_SCLK/QEI1.Z/SDM0.DAT1/ETH0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); also elsewhere on the board
PB30: U3.A5 (PB30/ESC0.CTR7/XPI0.CA_CS0/QEI1.A/SDM0.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); also elsewhere on the board
PB31: U3.B4 (PB31/ESC0.CTR8/XPI0.CA_D3/QEI1.B/SDM0.D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); also elsewhere on the board

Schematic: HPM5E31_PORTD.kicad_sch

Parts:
U3: HPM5E31IGN1; BGA-196_14x14_12.0x12.0mm_P0.8mm

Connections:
/ENCODER_CONN_A/ENC.A: U3.B13 (PD07/I2C3.SCL/ESC0.GPI24/ESC0.GPO39/PPI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); also elsewhere on the board
/ENCODER_CONN_A/ENC.B: U3.C12 (PD06/I2C3.SDA/ESC0.GPI25/ESC0.GPO38/PPI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); also elsewhere on the board
/ENCODER_CONN_A/ENC.Z: U3.B12 (PD05/MCAN1.TXD/ESC0.GPI26/ESC0.GPO37/PP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); also elsewhere on the board
/ENCODER_CONN_B/ENC.A: U3.K12 (PD30/ESC0.GPI01/ESC0.GPO62/PPI0.DQ01/ES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); also elsewhere on the board
/ENCODER_CONN_B/ENC.B: U3.K11 (PD31/ESC0.GPI00/ESC0.GPO63/PPI0.DQ00/ES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); also elsewhere on the board
/ENCODER_CONN_B/ENC.PWR: U3.F11 (PD13/I2C1.SCL/MCAN3.STBY/ESC0.GPI18/ESC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); also elsewhere on the board
/ENCODER_CONN_B/ENC.U: U3.F12 (PD12/I2C1.SDA/ESC0.GPI19/ESC0.GPO44/PPI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); also elsewhere on the board
/ENCODER_CONN_B/ENC.V: U3.E12 (PD10/MCAN2.STBY/ESC0.GPI21/ESC0.GPO42/P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); also elsewhere on the board
/ENCODER_CONN_B/ENC.W: U3.E11 (PD11/ESC0.GPI20/ESC0.GPO43/PPI0.CS2/PWM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); also elsewhere on the board
/ENCODER_CONN_B/ENC.Z: U3.J10 (PD29/ESC0.GPI02/ESC0.GPO61/PPI0.DQ02/ES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); also elsewhere on the board
/ETHERNET_PHY_P2/MII.RXC: U3.J13 (PD21/ESC0.GPI10/ESC0.GPO53/PPI0.DQ13/ES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); also elsewhere on the board
/ETHERNET_PHY_P2/MII.RXD0: U3.H14 (PD17/ESC0.GPI14/ESC0.GPO49/PPI0.DQ09/ES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); also elsewhere on the board
/ETHERNET_PHY_P2/MII.RXD1: U3.H13 (PD18/ESC0.GPI13/ESC0.GPO50/PPI0.DQ12/ES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); also elsewhere on the board
/ETHERNET_PHY_P2/MII.RXD2: U3.H12 (PD19/ESC0.GPI12/ESC0.GPO51/PPI0.DQ11/ES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); also elsewhere on the board
/ETHERNET_PHY_P2/MII.RXD3: U3.J14 (PD20/ESC0.GPI11/ESC0.GPO52/PPI0.DQ14/ES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); also elsewhere on the board
/ETHERNET_PHY_P2/MII.RX_DV: U3.G12 (PD16/ESC0.GPI15/ESC0.GPO48/PPI0.DQ10/ES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); also elsewhere on the board
/ETHERNET_PHY_P2/MII.RX_ER: U3.J12 (PD22/ESC0.GPI09/ESC0.GPO54/PPI0.DQ15/ES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); also elsewhere on the board
/ETHERNET_PHY_P2/MII.TXC: U3.F10 (PD23/ESC0.GPI08/ESC0.GPO55/PPI0.DM0/ESC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); also elsewhere on the board
/ETHERNET_PHY_P2/MII.TXD0: U3.G11 (PD24/ESC0.GPI07/ESC0.GPO56/PPI0.DQ06/ES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); also elsewhere on the board
/ETHERNET_PHY_P2/MII.TXD1: U3.G10 (PD25/ESC0.GPI06/ESC0.GPO57/PPI0.DQ07/ES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); also elsewhere on the board
/ETHERNET_PHY_P2/MII.TXD2: U3.H11 (PD26/ESC0.GPI05/ESC0.GPO58/PPI0.DQ05/ES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); also elsewhere on the board
/ETHERNET_PHY_P2/MII.TXD3: U3.H10 (PD27/ESC0.GPI04/ESC0.GPO59/PPI0.DQ04/ES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); also elsewhere on the board
/ETHERNET_PHY_P2/MII.TXEN: U3.J11 (PD28/ESC0.GPI03/ESC0.GPO60/PPI0.DQ03/ES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); also elsewhere on the board
/HPM5E31_TOP/CAN3.RXD: U3.G14 (PD14/MCAN3.RXD/ESC0.GPI17/ESC0.GPO46/PP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); also elsewhere on the board
/HPM5E31_TOP/CAN3.TXD: U3.G13 (PD15/MCAN3.TXD/ESC0.GPI16/ESC0.GPO47/PP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); also elsewhere on the board
PD0: U3.D9 (PD00/MCAN0.TXD/ESC0.GPI31/ESC0.GPO32/PP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)
PD1: U3.C10 (PD01/MCAN0.RXD/ESC0.GPI30/ESC0.GPO33/PP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); also elsewhere on the board
PD2: U3.D10 (PD02/I2C2.SCL/MCAN0.STBY/ESC0.GPI29/ESC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); also elsewhere on the board
PD3: U3.C11 (PD03/I2C2.SDA/MCAN1.STBY/ESC0.GPI28/ESC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); also elsewhere on the board
PD4: U3.D11 (PD04/MCAN1.RXD/ESC0.GPI27/ESC0.GPO36/PP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); also elsewhere on the board
PD8: U3.C13 (PD08/I2C0.SCL/MCAN2.TXD/ESC0.GPI23/ESC0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)
PD9: U3.D12 (PD09/I2C0.SDA/MCAN2.RXD/ESC0.GPI22/ESC0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); also elsewhere on the board

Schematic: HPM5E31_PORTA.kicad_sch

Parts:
C5, C6, C7, C8: 100nF,10V; C_0201_0603Metric
U3: HPM5E31IGN1; BGA-196_14x14_12.0x12.0mm_P0.8mm

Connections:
+3.3V: C5.1, C6.1, C7.1, C8.1, U3.E6 (VIO_B01), U3.E7 (VIO_B01), U3.E8 (VIO_B01), U3.E9 (VIO_B01), U3.K6 (VIO_B01); also elsewhere on the board
/ENCODER_CONN_A/ENC.PWR: U3.K2 (PA19/GPTMR3.CAPT1/UART4.CTS/SPI3.CS3/ES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); also elsewhere on the board
/ENCODER_CONN_A/ENC.U: U3.H1 (PA22/GPTMR2.CAPT0/UART5.RXD/SPI2.MISO/E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); also elsewhere on the board
/ENCODER_CONN_A/ENC.V: U3.J2 (PA21/GPTMR3.COMP2/UART5.DE/UART5.RTS/SP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); also elsewhere on the board
/ENCODER_CONN_A/ENC.W: U3.J1 (PA20/UART5.CTS/SPI2.SCLK/ESC0.P0_RXD3/S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); also elsewhere on the board
/ETHERNET_PHY_P0/MII.RX_ER: U3.H2 (PA23/GPTMR2.COMP0/UART5.TXD/SPI2.MOSI/E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); also elsewhere on the board
/ETHERNET_PHY_P2/MII.MDC: U3.H5 (PA31/GPTMR2.COMP3/UART7.TXD/SPI3.DAT3/E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); also elsewhere on the board
/ETHERNET_PHY_P2/MII.MDIO: U3.H4 (PA30/UART7.RXD/SPI3.DAT2/ESC0.MDIO/ETH0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); also elsewhere on the board
/HPM5E31_TOP/RS485_4.DE: U3.K1 (PA18/GPTMR3.COMP1/UART4.DE/UART4.RTS/ES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); also elsewhere on the board
/HPM5E31_TOP/RS485_4.DI: U3.L1 (PA16/GPTMR3.COMP0/UART4.TXD/ESC0.P0_RXD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); also elsewhere on the board
/HPM5E31_TOP/RS485_4.RO: U3.L2 (PA17/GPTMR3.CAPT0/UART4.RXD/ESC0.P0_RXD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); also elsewhere on the board
/HPM5E31_TOP/RS485_6.DE: U3.J3 (PA26/GPTMR2.COMP2/UART6.DE/UART6.RTS/SP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); also elsewhere on the board
/HPM5E31_TOP/RS485_6.DI: U3.K3 (PA24/GPTMR2.COMP1/UART6.TXD/SPI3.CS2/ES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); also elsewhere on the board
/HPM5E31_TOP/RS485_6.RO: U3.K4 (PA25/GPTMR2.CAPT1/UART6.RXD/SPI3.CS1/ES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); also elsewhere on the board
GND: C5.2, C6.2, C7.2, C8.2; also elsewhere on the board
PA0: U3.G2 (PA00/GPTMR1.COMP0/UART0.TXD/MCAN0.TXD/P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); also elsewhere on the board
PA1: U3.G3 (PA01/GPTMR1.CAPT0/UART0.RXD/MCAN0.RXD/P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); also elsewhere on the board
PA2: U3.G4 (PA02/GPTMR1.COMP1/UART0.DE/UART0.RTS/I2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); also elsewhere on the board
PA3: U3.G5 (PA03/GPTMR1.CAPT1/UART0.CTS/I2C2.SDA/MC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); also elsewhere on the board
PA4: U3.F2 (PA04/UART1.CTS/SPI1.SCLK/MCAN1.RXD/PWM0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); also elsewhere on the board
PA5: U3.F3 (PA05/GPTMR1.COMP2/UART1.DE/UART1.RTS/SP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); also elsewhere on the board
PA6: U3.F4 (PA06/GPTMR0.CAPT0/UART1.RXD/I2C3.SDA/SP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); also elsewhere on the board
PA7: U3.F5 (PA07/GPTMR0.COMP0/UART1.TXD/I2C3.SCL/SP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); also elsewhere on the board
PA8: U3.G1 (PA08/GPTMR0.COMP1/UART2.TXD/I2C0.SCL/MC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); also elsewhere on the board
PA9: U3.F1 (PA09/GPTMR0.CAPT1/UART2.RXD/I2C0.SDA/MC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); also elsewhere on the board
PA27: U3.J4 (PA27/UART6.CTS/SPI3.CS0/ESC0.P0_TXD2/QE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)
PA28: U3.J5 (PA28/UART7.CTS/SPI3.MISO/ESC0.P0_TXD3/E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)
PA29: U3.H3 (PA29/GPTMR3.COMP3/UART7.DE/UART7.RTS/SP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)

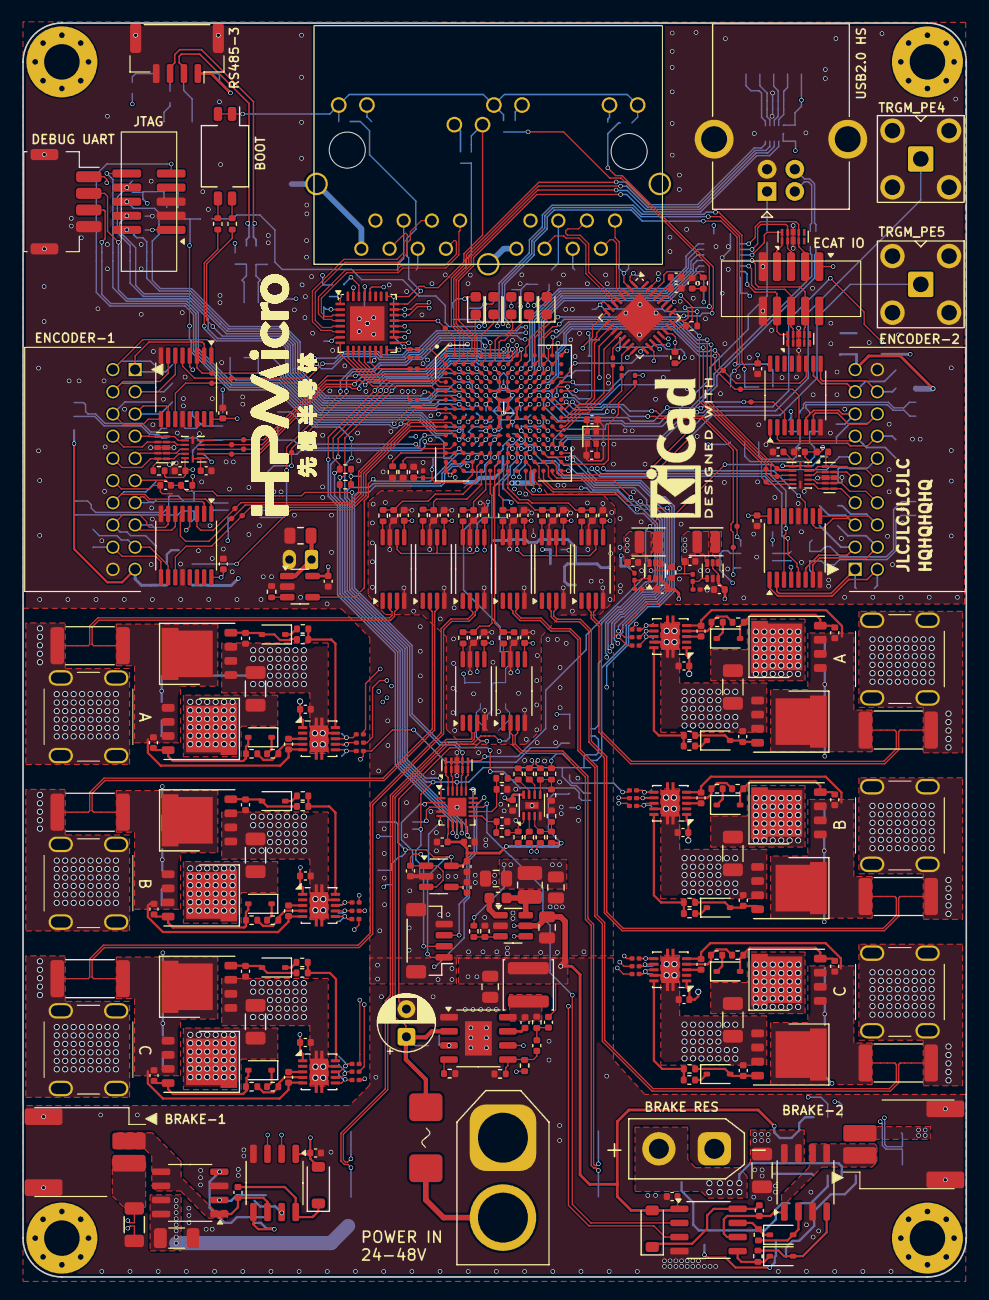
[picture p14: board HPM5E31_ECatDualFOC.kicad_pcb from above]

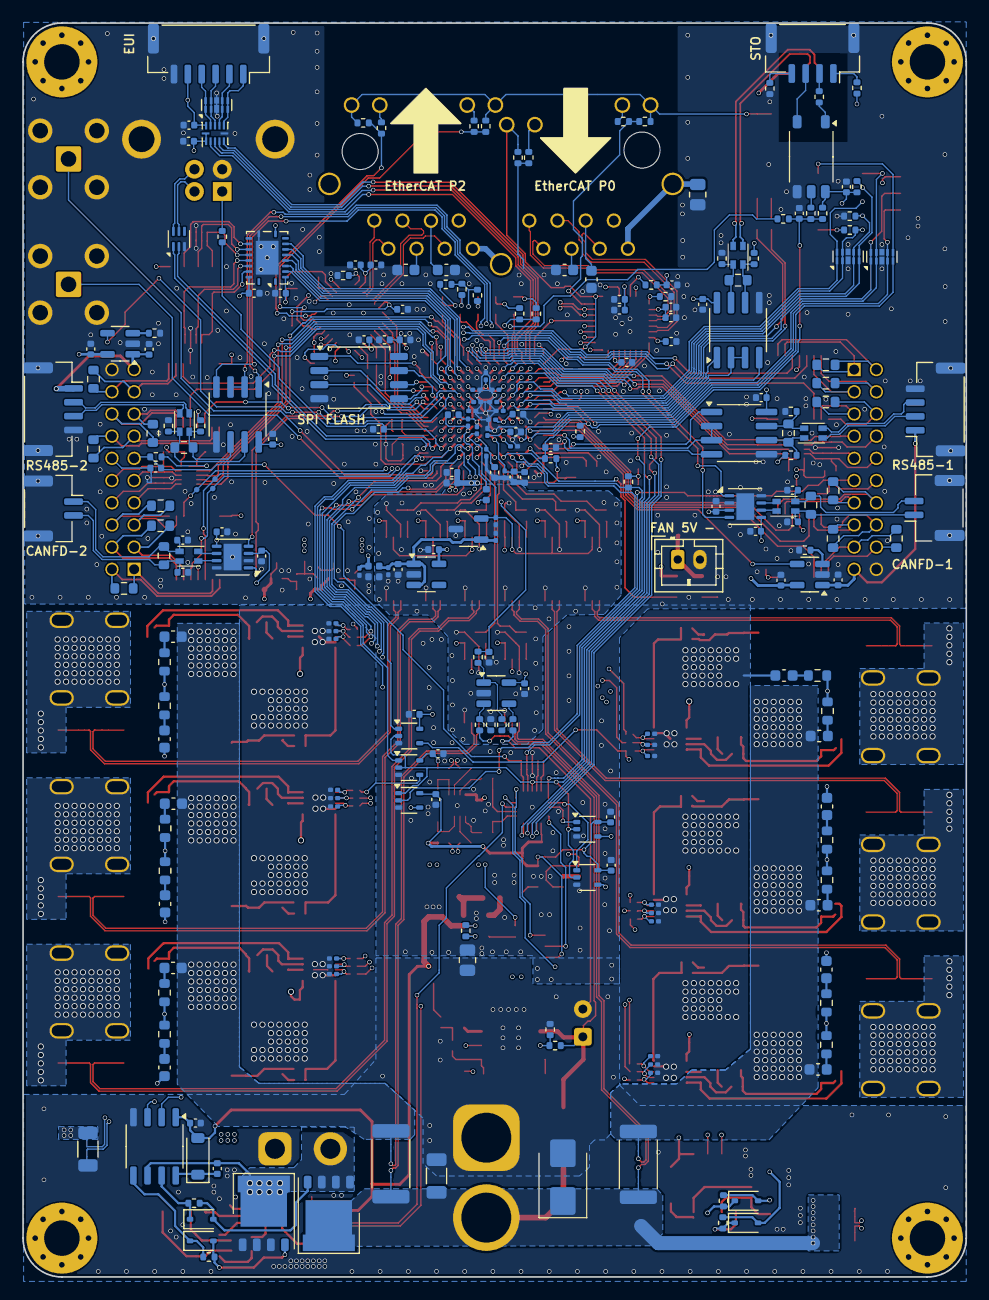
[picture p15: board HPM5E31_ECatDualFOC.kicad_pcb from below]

Board: 4 copper layers, 85.0 x 113.0 mm, 585 parts (250 on the bottom side), 455 nets.

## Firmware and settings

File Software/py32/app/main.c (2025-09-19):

#include "main.h"
#include "BrakeController.h"
#include "py32f002b_ll_adc.h"
#include "py32f002b_ll_bus.h"
#include "py32f002b_ll_exti.h"
#include "py32f002b_ll_gpio.h"
#include "py32f002b_ll_rcc.h"
#include "py32f002b_ll_system.h"
#include "py32f002b_ll_tim.h"
#include "py32f002b_ll_usart.h"
#include "py32f002b_ll_utils.h"
#include "py32f002bx5.h"
#include "system_py32f0xx.h"
#include "uart_dict.h"
#include <stdbool.h>
#include <stdint.h>

#ifdef RTT_ENABLE
#include "SEGGER_RTT.h"
#endif

static void SystemClockConfig(void);
void PWM_Init(void);
void GPIO_Init(void);
void USART_Init(void);
void ADC_Init(void);
void EXTI_Init(void);

void brake1_enable(bool enable, uint16_t duty);
void brake2_enable(bool enable, uint16_t duty);
void brake1_write_int_pin(bool state);
void brake2_write_int_pin(bool state);

BrakeController_t brake_controller[2];

volatile uint32_t delay_tick = 0;

static const struct
{
    uint32_t channel;
    uint32_t sampling_time;
} adc_ConvRank[] = {
    {LL_ADC_CHANNEL_7, LL_ADC_SAMPLINGTIME_13CYCLES_5},           //
    {LL_ADC_CHANNEL_0, LL_ADC_SAMPLINGTIME_13CYCLES_5},           //
    {LL_ADC_CHANNEL_1, LL_ADC_SAMPLINGTIME_71CYCLES_5},           //
    {LL_ADC_CHANNEL_2, LL_ADC_SAMPLINGTIME_71CYCLES_5},           //
    {LL_ADC_CHANNEL_TEMPSENSOR, LL_ADC_SAMPLINGTIME_239CYCLES_5}, //
};

uint8_t adc_rank_index = 0;

uint16_t adc_value[sizeof(adc_ConvRank) / sizeof(adc_ConvRank[0])] = {0};

void IncTick()
{
    if (delay_tick)
        delay_tick--;

    BrakeController(&brake_controller[0], BREAK_EV_TICK);
    BrakeController(&brake_controller[1], BREAK_EV_TICK);
}

#define CURRENT_TO_ADC(current) ((uint16_t)((current) * 4096 / 3.3f))

/**
 * @brief  Main program.
 * @retval int
 */
int main(void)
{
    SystemClockConfig();
    LL_APB1_GRP2_EnableClock(LL_APB1_GRP2_PERIPH_SYSCFG);
    LL_APB1_GRP1_EnableClock(LL_APB1_GRP1_PERIPH_PWR);
    LL_IOP_GRP1_EnableClock(LL_IOP_GRP1_PERIPH_GPIOA);
    LL_IOP_GRP1_EnableClock(LL_IOP_GRP1_PERIPH_GPIOB);
    LL_IOP_GRP1_EnableClock(LL_IOP_GRP1_PERIPH_GPIOC);

    GPIO_Init();
    EXTI_Init();
    USART_Init();
    ADC_Init();
    PWM_Init();

    brake_controller[0].brake_set_pwm_cb = brake1_enable;
    brake_controller[0].brake_write_int_pin = brake1_write_int_pin;
    brake_controller[0].index = UD_BRAKE1_CTRL;
    brake_controller[0].p_adc_value = &adc_value[0];

    brake_controller[1].brake_set_pwm_cb = brake2_enable;
    brake_controller[1].brake_write_int_pin = brake2_write_int_pin;
    brake_controller[1].index = UD_BRAKE2_CTRL;
    brake_controller[1].p_adc_value = &adc_value[1];

    uart_dict[UD_BRAKE1_CTRL] = UD_BRAKE_CTRL_FLAG_INIT_DONE;
    uart_dict[UD_BRAKE1_ON_DUTY] = 150;
    uart_dict[UD_BRAKE1_ON_TIME] = 200;
    uart_dict[UD_BRAKE1_ON_CURRENT] = CURRENT_TO_ADC(0.3f);
    uart_dict[UD_BRAKE1_HOLD_DUTY] = 100;
    uart_dict[UD_BRAKE1_HOLD_CURRENT] = CURRENT_TO_ADC(0.2f);
    uart_dict[UD_BRAKE1_OFF_TIME] = 100;

    uart_dict[UD_BRAKE2_CTRL] = UD_BRAKE_CTRL_FLAG_INIT_DONE;
    uart_dict[UD_BRAKE2_ON_DUTY] = 150;
    uart_dict[UD_BRAKE2_ON_TIME] = 200;
    uart_dict[UD_BRAKE2_ON_CURRENT] = CURRENT_TO_ADC(0.3f);
    uart_dict[UD_BRAKE2_HOLD_DUTY] = 100;
    uart_dict[UD_BRAKE2_HOLD_CURRENT] = CURRENT_TO_ADC(0.2f);
    uart_dict[UD_BRAKE2_OFF_TIME] = 100;

    delay_tick = 50;

    while (1)
    {
        uint32_t flag = uart_get_edit_flag();

        if (UART_DICT_HAS_FLAG(flag, UD_BRAKE1_CTRL))
        {
            if (uart_dict[UD_BRAKE1_CTRL] & UD_BRAKE_CTRL_FLAG_INIT_DONE)
            {
                if (uart_dict[UD_BRAKE1_CTRL] & UD_BRAKE_CTRL_FLAG_ENABLE)
                    BrakeController(&brake_controller[0], BREAK_EV_ENABLE);
                if (uart_dict[UD_BRAKE1_CTRL] & UD_BRAKE_CTRL_FLAG_DISABLE)
                    BrakeController(&brake_controller[0], BREAK_EV_DISABLE);
                CLEAR_BIT(uart_dict[UD_BRAKE1_CTRL], UD_BRAKE_CTRL_FLAG_ENABLE | UD_BRAKE_CTRL_FLAG_DISABLE);
            }
        }

        if (UART_DICT_HAS_FLAG(flag, UD_BRAKE2_CTRL))
        {
            if (uart_dict[UD_BRAKE2_CTRL] & UD_BRAKE_CTRL_FLAG_INIT_DONE)
            {
                if (uart_dict[UD_BRAKE2_CTRL] & UD_BRAKE_CTRL_FLAG_ENABLE)
                    BrakeController(&brake_controller[1], BREAK_EV_ENABLE);
                if (uart_dict[UD_BRAKE2_CTRL] & UD_BRAKE_CTRL_FLAG_DISABLE)
                    BrakeController(&brake_controller[1], BREAK_EV_DISABLE);
                CLEAR_BIT(uart_dict[UD_BRAKE2_CTRL], UD_BRAKE_CTRL_FLAG_ENABLE | UD_BRAKE_CTRL_FLAG_DISABLE);
            }
        }

        if (delay_tick == 0)
        {
            delay_tick = 50;
            uart_dict[UD_BRAKE1_CUR_CURRENT] = adc_value[0];
            uart_dict[UD_BRAKE2_CUR_CURRENT] = adc_value[1];
            uart_dict[UD_MOTOR1_TEMP_ADC] = adc_value[2];
            uart_dict[UD_MOTOR2_TEMP_ADC] = adc_value[3];
            uart_dict[UD_MCU_TEMP_ADC] = adc_value[4];
            uart_send_pdo(UD_STATUS, 6);
        }
    }
}

void EmergencyStop(void)
{
    BrakeController(&brake_controller[0], BREAK_EV_FAULT);
    BrakeController(&brake_controller[1], BREAK_EV_FAULT);
}

void brake1_enable(bool enable, uint16_t duty)
{
    if (enable)
    {
        LL_GPIO_SetOutputPin(GPIOB, LL_GPIO_PIN_7);
        LL_TIM_OC_SetCompareCH2(TIM1, duty);
    }
    else
    {
        LL_GPIO_ResetOutputPin(GPIOB, LL_GPIO_PIN_7);
        LL_TIM_OC_SetCompareCH2(TIM1, 0);
    }
}

void brake2_enable(bool enable, uint16_t duty)
{
    if (enable)
    {
        LL_GPIO_SetOutputPin(GPIOC, LL_GPIO_PIN_1);
        LL_TIM_OC_SetCompareCH1(TIM1, duty);
    }
    else
    {
        LL_GPIO_ResetOutputPin(GPIOC, LL_GPIO_PIN_1);
        LL_TIM_OC_SetCompareCH1(TIM1, 0);
    }
}

void brake1_write_int_pin(bool state)
{
    if (state)
    {
        LL_GPIO_ResetOutputPin(GPIOB, LL_GPIO_PIN_3);
        SET_BIT(uart_dict[UD_STATUS], UD_STATUS_FLAG_BRAKE1_OPENED);
    }
    else
    {
        LL_GPIO_SetOutputPin(GPIOB, LL_GPIO_PIN_3);
        CLEAR_BIT(uart_dict[UD_STATUS], UD_STATUS_FLAG_BRAKE1_OPENED);
    }
}

void brake2_write_int_pin(bool state)
{
    if (state)
    {
        LL_GPIO_ResetOutputPin(GPIOB, LL_GPIO_PIN_2);
        SET_BIT(uart_dict[UD_STATUS], UD_STATUS_FLAG_BRAKE2_OPENED);
    }
    else
    {
        LL_GPIO_SetOutputPin(GPIOB, LL_GPIO_PIN_2);
        CLEAR_BIT(uart_dict[UD_STATUS], UD_STATUS_FLAG_BRAKE2_OPENED);
    }
}

void ADC_IRQ_Callback(uint16_t value)
{
    adc_value[adc_rank_index] = value;
    adc_rank_index++;
    if (adc_rank_index >= sizeof(adc_ConvRank) / sizeof(adc_ConvRank[0]))
        adc_rank_index = 0;

    LL_ADC_REG_StopConversion(ADC1);
    LL_ADC_REG_SetSequencerChannels(ADC1, adc_ConvRank[adc_rank_index].channel);
    LL_ADC_SetSamplingTimeCommonChannels(ADC1, adc_ConvRank[adc_rank_index].sampling_time);
    LL_ADC_Enable(ADC1);
    LL_ADC_REG_StartConversion(ADC1);
}

void GPIO_Init(void)
{
    LL_GPIO_SetPinMode(GPIOB, LL_GPIO_PIN_7, LL_GPIO_MODE_OUTPUT);
    LL_GPIO_SetPinOutputType(GPIOB, LL_GPIO_PIN_7, LL_GPIO_OUTPUT_PUSHPULL);
    LL_GPIO_SetPinPull(GPIOB, LL_GPIO_PIN_7, LL_GPIO_PULL_NO);
    LL_GPIO_SetPinSpeed(GPIOB, LL_GPIO_PIN_7, LL_GPIO_SPEED_FREQ_HIGH);

    LL_GPIO_SetPinMode(GPIOB, LL_GPIO_PIN_7, LL_GPIO_MODE_OUTPUT);
    LL_GPIO_SetPinOutputType(GPIOB, LL_GPIO_PIN_7, LL_GPIO_OUTPUT_PUSHPULL);
    LL_GPIO_SetPinPull(GPIOB, LL_GPIO_PIN_7, LL_GPIO_PULL_NO);
    LL_GPIO_SetPinSpeed(GPIOB, LL_GPIO_PIN_7, LL_GPIO_SPEED_FREQ_HIGH);
}

void EXTI_Init()
{
    LL_GPIO_InitTypeDef GPIO_InitStruct = {0};
    LL_EXTI_InitTypeDef EXTI_InitStruct = {0};

    GPIO_InitStruct.Pin = LL_GPIO_PIN_5;
    GPIO_InitStruct.Mode = LL_GPIO_MODE_INPUT;
    GPIO_InitStruct.Pull = LL_GPIO_PULL_NO;
    LL_GPIO_Init(GPIOA, &GPIO_InitStruct);
    LL_EXTI_SetEXTISource(LL_EXTI_CONFIG_PORTA, LL_EXTI_CONFIG_LINE5);
    LL_SYSCFG_EnableGPIOFilter(LL_SYSCFG_GPIO_PORTA, LL_GPIO_PIN_5);

    EXTI_InitStruct.Line = LL_EXTI_LINE_5;
    EXTI_InitStruct.LineCommand = ENABLE;
    EXTI_InitStruct.Mode = LL_EXTI_MODE_IT;
    EXTI_InitStruct.Trigger = LL_EXTI_TRIGGER_FALLING;
    LL_EXTI_Init(&EXTI_InitStruct);

    NVIC_SetPriority(EXTI4_15_IRQn, 0);
    NVIC_EnableIRQ(EXTI4_15_IRQn);
}

void USART_Init(void)
{
    LL_USART_InitTypeDef USART_InitStruct = {0};
    LL_GPIO_InitTypeDef GPIO_InitStruct = {0};
    LL_APB1_GRP2_EnableClock(LL_APB1_GRP2_PERIPH_USART1);

    GPIO_InitStruct.Pin = LL_GPIO_PIN_4;
    GPIO_InitStruct.Mode = LL_GPIO_MODE_ALTERNATE;
    GPIO_InitStruct.Speed = LL_GPIO_SPEED_FREQ_VERY_HIGH;
    GPIO_InitStruct.OutputType = LL_GPIO_OUTPUT_PUSHPULL;
    GPIO_InitStruct.Pull = LL_GPIO_PULL_UP;
    GPIO_InitStruct.Alternate = LL_GPIO_AF1_USART1;
    LL_GPIO_Init(GPIOB, &GPIO_InitStruct);

    GPIO_InitStruct.Pin = LL_GPIO_PIN_5;
    GPIO_InitStruct.Alternate = LL_GPIO_AF1_USART1;
    LL_GPIO_Init(GPIOB, &GPIO_InitStruct);

    USART_InitStruct.BaudRate = 115200;
    USART_InitStruct.DataWidth = LL_USART_DATAWIDTH_8B;
    USART_InitStruct.StopBits = LL_USART_STOPBITS_1;
    USART_InitStruct.Parity = LL_USART_PARITY_NONE;
    USART_InitStruct.TransferDirection = LL_USART_DIRECTION_TX_RX;
    USART_InitStruct.HardwareFlowControl = LL_USART_HWCONTROL_NONE;
    USART_InitStruct.OverSampling = LL_USART_OVERSAMPLING_16;
    LL_USART_Init(USART1, &USART_InitStruct);

    LL_USART_ConfigAsyncMode(USART1);
    LL_USART_EnableIT_RXNE(USART1);
    LL_USART_EnableIT_IDLE(USART1);
    
    NVIC_SetPriority(USART1_IRQn, 1);
    NVIC_EnableIRQ(USART1_IRQn);
    LL_USART_Enable(USART1);
}

void PWM_Init(void)
{
    LL_GPIO_InitTypeDef GPIO_InitStruct = {0};

    LL_APB1_GRP2_EnableClock(LL_APB1_GRP2_PERIPH_TIM1);

    GPIO_InitStruct.Pin = LL_GPIO_PIN_0 | LL_GPIO_PIN_1;
    GPIO_InitStruct.Mode = LL_GPIO_MODE_ALTERNATE;
    GPIO_InitStruct.Pull = LL_GPIO_PULL_NO;
    GPIO_InitStruct.Speed = LL_GPIO_SPEED_FREQ_HIGH;
    GPIO_InitStruct.Alternate = LL_GPIO_AF2_TIM1;
    LL_GPIO_Init(GPIOA, &GPIO_InitStruct);

    LL_TIM_SetCounterMode(TIM1, LL_TIM_COUNTERMODE_CENTER_UP);
    LL_TIM_SetAutoReload(TIM1, 300 - 1);
    LL_TIM_SetPrescaler(TIM1, 0);
    LL_TIM_SetClockDivision(TIM1, LL_TIM_CLOCKDIVISION_DIV1);
    LL_TIM_SetRepetitionCounter(TIM1, 80 - 1);
    LL_TIM_EnableARRPreload(TIM1);

    LL_TIM_OC_SetMode(TIM1, LL_TIM_CHANNEL_CH1, LL_TIM_OCMODE_PWM1);
    LL_TIM_OC_SetPolarity(TIM1, LL_TIM_CHANNEL_CH1, LL_TIM_OCPOLARITY_HIGH);
    LL_TIM_OC_SetCompareCH1(TIM1, 0);
    LL_TIM_OC_EnablePreload(TIM1, LL_TIM_CHANNEL_CH1);

    LL_TIM_OC_SetMode(TIM1, LL_TIM_CHANNEL_CH2, LL_TIM_OCMODE_PWM1);
    LL_TIM_OC_SetPolarity(TIM1, LL_TIM_CHANNEL_CH2, LL_TIM_OCPOLARITY_HIGH);
    LL_TIM_OC_SetCompareCH2(TIM1, 0);
    LL_TIM_OC_EnablePreload(TIM1, LL_TIM_CHANNEL_CH2);

    LL_TIM_SetTriggerOutput(TIM1, LL_TIM_TRGO_UPDATE);

    LL_TIM_EnableAllOutputs(TIM1);
    LL_TIM_EnableCounter(TIM1);
    LL_TIM_CC_EnableChannel(TIM1, LL_TIM_CHANNEL_CH1 | LL_TIM_CHANNEL_CH2);
}

void ADC_Init(void)
{
    LL_GPIO_InitTypeDef GPIO_InitStruct = {0};
    LL_ADC_InitTypeDef ADC_InitStruct = {0};
    LL_ADC_REG_InitTypeDef ADC_REG_InitStruct = {0};

    LL_APB1_GRP2_EnableClock(LL_APB1_GRP2_PERIPH_ADC1);

    GPIO_InitStruct.Mode = LL_GPIO_MODE_ANALOG;
    GPIO_InitStruct.Pull = LL_GPIO_PULL_NO;

    GPIO_InitStruct.Pin = LL_GPIO_PIN_3 | LL_GPIO_PIN_4 | LL_GPIO_PIN_6 | LL_GPIO_PIN_7;
    LL_GPIO_Init(GPIOA, &GPIO_InitStruct);

    GPIO_InitStruct.Pin = LL_GPIO_PIN_0 | LL_GPIO_PIN_1;
    LL_GPIO_Init(GPIOB, &GPIO_InitStruct);

    ADC_InitStruct.Clock = LL_ADC_CLOCK_SYNC_PCLK_DIV4;
    ADC_InitStruct.Resolution = LL_ADC_RESOLUTION_12B;
    ADC_InitStruct.DataAlignment = LL_ADC_DATA_ALIGN_RIGHT;
    ADC_InitStruct.LowPowerMode = LL_ADC_LP_MODE_NONE;
    LL_ADC_Init(ADC1, &ADC_InitStruct);

    ADC_REG_InitStruct.TriggerSource = LL_ADC_REG_TRIG_EXT_TIM1_TRGO;
    ADC_REG_InitStruct.SequencerDiscont = LL_ADC_REG_SEQ_DISCONT_1RANK;
    ADC_REG_InitStruct.ContinuousMode = LL_ADC_REG_CONV_SINGLE;
    ADC_REG_InitStruct.Overrun = LL_ADC_REG_OVR_DATA_OVERWRITTEN;
    LL_ADC_REG_Init(ADC1, &ADC_REG_InitStruct);
    LL_ADC_REG_SetTriggerEdge(ADC1, LL_ADC_REG_TRIG_EXT_RISING);

    LL_ADC_SetCommonPathInternalCh(__LL_ADC_COMMON_INSTANCE(ADC1), LL_ADC_PATH_INTERNAL_TEMPSENSOR);
    LL_ADC_REG_SetSequencerChannels(ADC1, adc_ConvRank[0].channel);

    volatile uint32_t wait_loop_index = ((LL_ADC_DELAY_TEMPSENSOR_STAB_US * (SystemCoreClock / (100000 * 2))) / 10);
    while (wait_loop_index != 0)
    {
        wait_loop_index--;
    }

    /* Enable EOC IT */
    LL_ADC_EnableIT_EOS(ADC1);

    NVIC_SetPriority(ADC_COMP_IRQn, 3);
    NVIC_EnableIRQ(ADC_COMP_IRQn);

    LL_ADC_StartCalibration(ADC1);
    while (LL_ADC_IsCalibrationOnGoing(ADC1))
    {
    }

    delay_tick = 2;
    while (delay_tick == 0)
        ;

    LL_ADC_Enable(ADC1);

    delay_tick = 2;
    while (delay_tick == 0)
        ;

    LL_ADC_REG_StartConversion(ADC1);
}

static void SystemClockConfig(void)
{
    /* Enable HSI */
    LL_RCC_HSI_Enable();
    while (LL_RCC_HSI_IsReady() != 1)
    {
    }

    /* Set AHB divider: HCLK = SYSCLK */
    LL_RCC_SetAHBPrescaler(LL_RCC_SYSCLK_DIV_1);

    /* HSISYS used as SYSCLK clock source  */
    LL_RCC_SetSysClkSource(LL_RCC_SYS_CLKSOURCE_HSISYS);
    while (LL_RCC_GetSysClkSource() != LL_RCC_SYS_CLKSOURCE_STATUS_HSISYS)
    {
    }

    /* Set APB1 divider */
    LL_RCC_SetAPB1Prescaler(LL_RCC_APB1_DIV_1);
    LL_Init1msTick(24000000);
    SysTick->CTRL |= SysTick_CTRL_TICKINT_Msk;

    NVIC_SetPriority(SysTick_IRQn, 15);
    NVIC_EnableIRQ(SysTick_IRQn);

    /* Update CMSIS variable (which can be updated also through SystemCoreClockUpdate function) */
    LL_SetSystemCoreClock(24000000);
}

/**
 * @brief  Error executing function.
 * @param  None
 * @retval None
 */
void APP_ErrorHandler(void)
{
    while (1)
    {
    }
}

#ifdef USE_FULL_ASSERT
/**
 * @brief  Reports the name of the source file and the source line number
 *         where the assert_param error has occurred.
 * @param  file: pointer to the source file name
 * @param  line: assert_param error line source number
 * @retval None
 */
void assert_failed(uint8_t *file, uint32_t line)
{
    /* Users can add their own printing information as needed,
       for example: printf("Wrong parameters value: file %s on line %d\r\n", file, line) */
    /* Infinite loop */
    while (1)
    {
    }
}
#endif /* USE_FULL_ASSERT */

/************************ (C) COPYRIGHT Puya *****END OF FILE******************/

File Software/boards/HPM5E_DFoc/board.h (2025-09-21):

/*
 * Copyright (c) 2025 HPMicro
 *
 * SPDX-License-Identifier: BSD-3-Clause
 *
 */

#ifndef _HPM_BOARD_H
#define _HPM_BOARD_H
#include <stdio.h>
#include "hpm_common.h"
#include "hpm_soc.h"
#include "hpm_soc_feature.h"
#include "hpm_clock_drv.h"
#include "pinmux.h"
#include "hpm_trgm_drv.h"
#include "hpm_gptmr_drv.h"
#if !defined(CONFIG_NDEBUG_CONSOLE) || !CONFIG_NDEBUG_CONSOLE
#include "hpm_debug_console.h"
#endif

#define BOARD_NAME          "HPM5E_DFoc"
#define BOARD_UF2_SIGNATURE (0x0A4D5048UL)
#define BOARD_CPU_FREQ      (480000000UL)

#define SEC_CORE_IMG_START CORE1_ILM_LOCAL_BASE

#ifndef BOARD_RUNNING_CORE
#define BOARD_RUNNING_CORE HPM_CORE0
#endif

/* ACMP desction */
#define BOARD_ACMP             HPM_ACMP0
#define BOARD_ACMP_CLK         clock_acmp0
#define BOARD_ACMP_CHANNEL     ACMP_CHANNEL_CHN1
#define BOARD_ACMP_IRQ         IRQn_ACMP0_1
#define BOARD_ACMP_PLUS_INPUT  ACMP_INPUT_DAC_OUT  /* use internal DAC */
#define BOARD_ACMP_MINUS_INPUT ACMP_INPUT_ANALOG_6 /* align with used pin */

/* uart section */
#define BOARD_APP_UART_BASE       HPM_UART4
#define BOARD_APP_UART_IRQ        IRQn_UART4
#define BOARD_APP_UART_BAUDRATE   (115200UL)
#define BOARD_APP_UART_CLK_NAME   clock_uart4
#define BOARD_APP_UART_RX_DMA_REQ HPM_DMA_SRC_UART4_RX
#define BOARD_APP_UART_TX_DMA_REQ HPM_DMA_SRC_UART4_TX

#define BOARD_APP_UART_BREAK_SIGNAL_PIN IOC_PAD_PD13

/* Trigger UART: UART0~3 use HPM_TRGM0_OUTPUT_SRC_UART_TRIG0, UART4~7 use HPM_TRGM0_OUTPUT_SRC_UART_TRIG1 */
#define BOARD_APP_UART_TRIG         HPM_TRGM0_OUTPUT_SRC_UART_TRIG1
#define BOARD_UART_TRGM             HPM_TRGM0
#define BOARD_UART_TRGM_GPTMR       HPM_GPTMR3
#define BOARD_UART_TRGM_GPTMR_CLK   clock_gptmr3
#define BOARD_UART_TRGM_GPTMR_CH    2
#define BOARD_UART_TRGM_GPTMR_INPUT HPM_TRGM0_INPUT_SRC_GPTMR3_OUT2

/* uart rx idle demo section */
#define BOARD_UART_IDLE            BOARD_APP_UART_BASE
#define BOARD_UART_IDLE_IRQ        BOARD_APP_UART_IRQ
#define BOARD_UART_IDLE_CLK_NAME   BOARD_APP_UART_CLK_NAME
#define BOARD_UART_IDLE_TX_DMA_SRC BOARD_APP_UART_TX_DMA_REQ
#define BOARD_UART_IDLE_DMA_SRC    BOARD_APP_UART_RX_DMA_REQ

#define BOARD_UART_IDLE_GPTMR          HPM_GPTMR3
#define BOARD_UART_IDLE_GPTMR_CLK_NAME clock_gptmr3
#define BOARD_UART_IDLE_GPTMR_IRQ      IRQn_GPTMR3
#define BOARD_UART_IDLE_GPTMR_CMP_CH   0
#define BOARD_UART_IDLE_GPTMR_CAP_CH   2

/* uart microros sample section */
#define BOARD_MICROROS_UART_BASE     BOARD_APP_UART_BASE
#define BOARD_MICROROS_UART_IRQ      BOARD_APP_UART_IRQ
#define BOARD_MICROROS_UART_CLK_NAME BOARD_APP_UART_CLK_NAME

/* usb cdc acm uart section */
#define BOARD_USB_CDC_ACM_UART            BOARD_APP_UART_BASE
#define BOARD_USB_CDC_ACM_UART_CLK_NAME   BOARD_APP_UART_CLK_NAME
#define BOARD_USB_CDC_ACM_UART_TX_DMA_SRC BOARD_APP_UART_TX_DMA_REQ
#define BOARD_USB_CDC_ACM_UART_RX_DMA_SRC BOARD_APP_UART_RX_DMA_REQ

/* uart lin sample section */
#define BOARD_UART_LIN                 BOARD_APP_UART_BASE
#define BOARD_UART_LIN_IRQ             BOARD_APP_UART_IRQ
#define BOARD_UART_LIN_CLK_NAME        BOARD_APP_UART_CLK_NAME
#define BOARD_UART_LIN_TX_PORT         GPIO_DI_GPIOC
#define BOARD_UART_LIN_TX_PIN          (16U)                         /* PC16 should align with used pin in pinmux configuration */
#define BOARD_UART_LIN_PLB_TRGM_IN_SRC HPM_TRGM0_INPUT_SRC_TRGM0_P05 /* align with used pin in pinmux configuration */

/* plb lin baudrate detection */
#define BOARD_PLB_TRGM_FILTER_GPIO_INPUT0 HPM_TRGM0_FILTER_SRC_TRGM0_P00
#define BOARD_PLB_TRGM_DMA_REQ0           HPM_TRGM0_DMA_SRC_TRGM_0

#if !defined(CONFIG_NDEBUG_CONSOLE) || !CONFIG_NDEBUG_CONSOLE
#ifndef BOARD_CONSOLE_TYPE
#define BOARD_CONSOLE_TYPE CONSOLE_TYPE_UART
#endif

#if BOARD_CONSOLE_TYPE == CONSOLE_TYPE_UART
#ifndef BOARD_CONSOLE_UART_BASE
#if BOARD_RUNNING_CORE == HPM_CORE0
#define BOARD_CONSOLE_UART_BASE       HPM_UART0
#define BOARD_CONSOLE_UART_CLK_NAME   clock_uart0
#define BOARD_CONSOLE_UART_IRQ        IRQn_UART0
#define BOARD_CONSOLE_UART_TX_DMA_REQ HPM_DMA_SRC_UART0_TX
#define BOARD_CONSOLE_UART_RX_DMA_REQ HPM_DMA_SRC_UART0_RX
#else
#define BOARD_CONSOLE_UART_BASE       HPM_UART11
#define BOARD_CONSOLE_UART_CLK_NAME   clock_uart11
#define BOARD_CONSOLE_UART_IRQ        IRQn_UART11
#define BOARD_CONSOLE_UART_TX_DMA_REQ HPM_DMA_SRC_UART11_TX
#define BOARD_CONSOLE_UART_RX_DMA_REQ HPM_DMA_SRC_UART11_RX
#endif
#endif
#define BOARD_CONSOLE_UART_BAUDRATE (115200UL)
#endif
#endif

/* rtthread-nano finsh section */
#define BOARD_RT_CONSOLE_BASE     BOARD_CONSOLE_UART_BASE
#define BOARD_RT_CONSOLE_CLK_NAME BOARD_CONSOLE_UART_CLK_NAME
#define BOARD_RT_CONSOLE_IRQ      BOARD_CONSOLE_UART_IRQ

/* modbus sample section */
#define BOARD_MODBUS_UART_BASE       BOARD_APP_UART_BASE
#define BOARD_MODBUS_UART_CLK_NAME   BOARD_APP_UART_CLK_NAME
#define BOARD_MODBUS_UART_RX_DMA_REQ BOARD_APP_UART_RX_DMA_REQ
#define BOARD_MODBUS_UART_TX_DMA_REQ BOARD_APP_UART_TX_DMA_REQ
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

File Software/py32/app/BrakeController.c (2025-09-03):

#include "BrakeController.h"
#include "uart_dict.h"
#include <stdint.h>

#define MAX_FAULT_TICKS 100

bool BrakeController_CheckCurrent(BrakeController_t *self)
{
    if (self->state == BRAKE_ST_HOLD)
    {
        if ((*self->p_adc_value - 2048) < uart_dict[self->index + UD_BRAKE1_HOLD_CURRENT])
        {
            if (self->cur_fault_tick < MAX_FAULT_TICKS)
            {
                self->cur_fault_tick++;
            }
            else
            {
                return false;
            }
        }
        else
        {
            self->cur_fault_tick = 0;
        }
    }
    else if (self->state == BRAKE_ST_UNLOCKING)
    {
        if ((*self->p_adc_value - 2048) < uart_dict[self->index + UD_BRAKE1_ON_CURRENT])
        {
            if (self->cur_fault_tick < MAX_FAULT_TICKS)
            {
                self->cur_fault_tick++;
            }
            else
            {
                return false;
            }
        }
        else
        {
            self->cur_fault_tick = 0;
        }
    }
    else
    {
        self->cur_fault_tick = 0;
    }
    return true;
}

void BrakeController(BrakeController_t *self, BrakeEvent_t event)
{
    if (event == BREAK_EV_TICK && !BrakeController_CheckCurrent(self))
    {
        event = BREAK_EV_FAULT;
    }

    if (event == BREAK_EV_FAULT)
    {
        if (self->state != BRAKE_ST_IDLE)
        {
            self->brake_set_pwm_cb(false, 0);
            self->brake_write_int_pin(false);
            self->state = BRAKE_ST_IDLE;
        }
        return;
    }

    switch (self->state)
    {
    case BRAKE_ST_IDLE:
        if (event == BREAK_EV_ENABLE)
        {
            self->brake_set_pwm_cb(true, uart_dict[self->index + UD_BRAKE1_ON_DUTY]);
            self->delay_tick = uart_dict[self->index + UD_BRAKE1_ON_TIME];
            self->state = BRAKE_ST_UNLOCKING;
        }
        // else
        // {
        //     self->brake_set_pwm_cb(false, 0);
        //     self->brake_write_int_pin(false);
        // }
        break;
    case BRAKE_ST_UNLOCKING:
        if (event == BREAK_EV_DISABLE)
        {
            self->state = BRAKE_ST_LOCKING;
            self->delay_tick = uart_dict[self->index + UD_BRAKE1_OFF_TIME];
            self->brake_write_int_pin(false);
            self->brake_set_pwm_cb(false, 0);
        }
        else if (self->delay_tick-- == 0)
        {
            self->brake_set_pwm_cb(true, uart_dict[self->index + UD_BRAKE1_HOLD_DUTY]);
            self->brake_write_int_pin(true);
            self->state = BRAKE_ST_HOLD;
        }
        break;
    case BRAKE_ST_HOLD:
        if (event == BREAK_EV_DISABLE)
        {
            self->state = BRAKE_ST_LOCKING;
            self->delay_tick = uart_dict[self->index + UD_BRAKE1_OFF_TIME];
            self->brake_write_int_pin(false);
            self->brake_set_pwm_cb(false, 0);
        }
        break;
    case BRAKE_ST_LOCKING:
        if (event == BREAK_EV_ENABLE)
        {
            self->brake_set_pwm_cb(true, uart_dict[self->index + UD_BRAKE1_ON_DUTY]);
            self->delay_tick = uart_dict[self->index + UD_BRAKE1_ON_TIME];
            self->state = BRAKE_ST_UNLOCKING;
        }
        else if (self->delay_tick-- == 0)
        {
            self->brake_set_pwm_cb(false, 0);
            self->brake_write_int_pin(false);
            self->state = BRAKE_ST_IDLE;
        }
        break;
    }
}

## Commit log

2025-06-25 新增ESC IO引出，ESC CTR LED，EUI接口
    编码器接口电源输出加保险，SPI加ESD
    PY32ADC外部接口加ESD
    [BREAK_MCU.kicad_sch, ENCODER_CONN.kicad_sch, ETHERNET_PHY.kicad_sch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]
2025-06-27 调整引脚，拉线
    [BREAK_MCU.kicad_sch, ETHERNET_PHY.kicad_sch, HPM5E31_ECatDualFOC.kicad_pcb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]
2025-07-07 修存档拉线
    [BREAK_MCU.kicad_sch, EMS_BUTTON.kicad_sch, ENCODER_CONN.kicad_sch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]
2025-07-13 拉线，增加刹车电阻
    [BRAKE_RES.kicad_sch, BREAK_MCU.kicad_sch, ENCODER_CONN.kicad_sch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]
2025-08-04 拉线，删除电荷泵，修改10Vdcdc斜坡补偿
    [BRAKE_RES.kicad_sch, BREAK_MCU.kicad_sch, ETHERNET_PHY.kicad_sch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]
2025-08-17 添加母线电压测量
    [BREAK_MCU.kicad_sch, ETHERNET_PHY.kicad_sch, HPM5E31_ECatDualFOC.kicad_pcb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]
2025-08-17 修饰，第一次打板
    [BRAKE_RES.kicad_sch, BREAK_MCU.kicad_sch, EMS_BUTTON.kicad_sch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]
2025-09-03 修改PCB，上传py32抱闸驱动代码，上传HPM board
    调整抱闸驱动栅极电阻
    急停光耦增加上拉电阻和滤波电路
    [BREAK_MCU.kicad_sch, EMS_BUTTON.kicad_sch, ETHERNET_PHY.kicad_sch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]
2025-09-19 PCB和foc_demo
    PCB：
    部分信号增加测试点
    半桥增加栅极电容和RC吸收（待定），泄放mos是否需要栅极电容待测
    软件：
    增加foc_demo半成品
    [BREAK_MCU.kicad_sch, ENCODER_CONN.kicad_sch, ETHERNET_PHY.kicad_sch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]
2025-09-21 foc_demo: pwm和adc功能补全，强拖和基本电流采样功能跑通
2025-10-01 初步实现电流环
    新增vofa协议实现
    pwm补全强制输出控制
    支持电流校准，电流采样序列切换
2025-10-03 PCB优化，修改母线电流采样电阻为2mR，栅极驱动器输入pwm增加滤波防干扰，其他少量优化
    [BREAK_MCU.kicad_sch, ETHERNET_PHY.kicad_sch, HPM5E31_ECatDualFOC.kicad_pcb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]
2025-10-05 PCB修改栅极电阻，增加上侧RC吸收电路，同步修改软件死区时间到150ns
    [BRAKE_RES.kicad_sch, BREAK_MCU.kicad_sch, ETHERNET_PHY.kicad_sch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]
2025-10-05 PCB：网口替换为HR911205C
    [BREAK_MCU.kicad_sch, ETHERNET_PHY.kicad_sch, HPM5E31_ECatDualFOC.kicad_pcb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]
2025-10-08 更改网口接地，更改RC吸收封装
    [BREAK_MCU.kicad_sch, ETHERNET_PHY.kicad_sch, HPM5E31_ECatDualFOC.kicad_pcb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]
2025-10-09 相线铜箔增加开窗
    [HPM5E31_ECatDualFOC.kicad_pcb]
2025-10-12 Update README with product specs and images
    Added product specifications, power tree, and hardware architecture sections to README.md. Included three new images in README.assets and updated instructions regarding JLink version requirements.
2025-10-12 PCB：风扇增加控制IO，泄放驱动增加使能引脚，485编码器电源接入控制
    [BREAK_MCU.kicad_sch, ENCODER_CONN.kicad_sch, ETHERNET_PHY.kicad_sch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]
2025-10-12 readme框图补全风扇开关
